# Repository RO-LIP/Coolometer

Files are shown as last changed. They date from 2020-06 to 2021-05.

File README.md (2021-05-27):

# Coolometer

A device, [inspired by Futurama](https://www.youtube.com/watch?v=tXb7gLe0zNk), to measure your coolness with a "real" AI.

## Components

This are the components we used. Alternatives might work also

- Raspberry PI Model 3 B+
- Raspberry PI Camera
- Micro Servo SG90
- MAX 4218CNG LED Matrix
- L9110 Motor Driver
- DC Motor 3V 16500 RPM 0.35A 130 Type
- Pizzo Speaker
- 3.5 mm Headphone Jack
- LY591-4 speaker
- PAM8403 Mini Amplifier
- Button
- 5V 2.1 A PowerBank for Power supply

### Wiring

Raspberry PI Model 3 B+ has enough ground Pins for all parts. Only one 5V pin has to be shared by the LED Matrix and the Servo motor.

<p align="center">
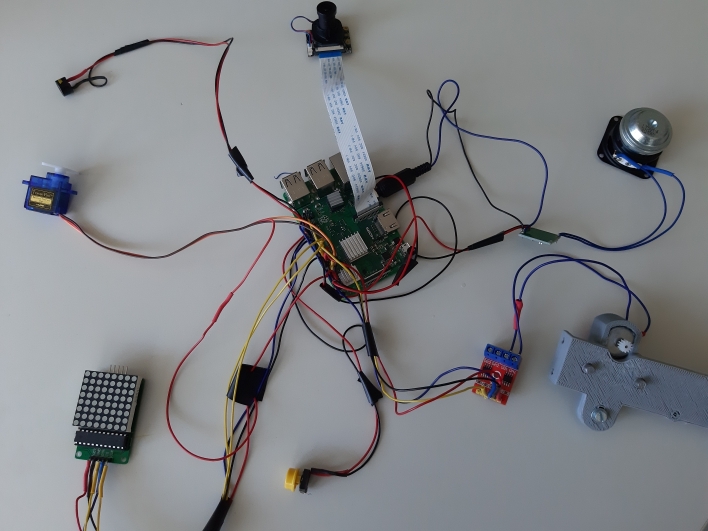
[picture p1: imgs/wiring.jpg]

</p>

#### Micro Servo SG90
One 5V shared with MAX 4218CNG LED Matrix<br/>
Data on GPIO 17 / PIN 11

#### MAX 4218CNG LED Matrix
One 5V shared with MAX 4218CNG LED Matrix<br/>
DIN on GPIO 10 / PIN 19<br/>
CS on GPIO 8 / PIN 24<br/>
CLK on GPIO 11 / PIN 23

#### L9110 Motor Driver
VCC on 3.3 <br/>
IA1 on GPIO 26 / PIN 37<br/>
IB1 on GPIO 20 / PIN 38

#### Pizzo Speaker
VCC on 3.3<br/>
GND on GPIO 36 / PIN 16

#### Headphone Jack / Amplifier
The Headphone Jack uses the Audio Out from the Raspberry PI.<br/>
Solder the longest PIN of the Jack to the "I" PIN of the Amplifier Board
Solder the second longest PIN longest PIN of the Jack to the "R" PIN of the Amplifier Board. We only use one Channel here.

Solder the R OUT PINs the the speaker.

Use one 5V Pin from the Raspberry PI to power the Amplifier Board

#### Button
VCC on 3.3 <br/>
GND to GPIO 18 / PIN 12

#### Camera
The camera is connected on the Raspberry Camera slot.

## Install
Set up a Raspberry PI with [Raspberry Pi OS Lite](https://www.raspberrypi.org/software/operating-systems/) 
[Enable SSH](https://www.raspberrypi.org/documentation/remote-access/ssh/) and connect via SSH to the Raspberry
Update System ( sudo apt full-upgrade)
Run sudo raspi-config:
- ADVANCED -> Resize File System
- SYSTEM  -> AUDIO -> Headphone Jack
- Interface -> Camera -> ON
- Interface -> SPI -> ON

Set System volume with 
```bash
sudo amixer -q -M sset Headphone 100%
```
Install depenendices:
```bash
sudo apt-get install python3-pip python3-venv python3-pygame 
libfreetype6-dev libjpeg-dev libopenjp2-7 libtiff5 libjpeg-dev libtiff5-dev libjasper-dev 
libpng12-dev libavcodec-dev libavformat-dev libswscale-dev 
libv4l-dev libxvidcore-dev libx264-dev qt4-dev-tools libatlas-base-dev 
libilmbase-dev libopenexr-dev libgstreamer1.0-dev libgirepository1.0-dev libcairo2-dev
```

Install Python dependencies:
```bash
python3 -m pip install --user --upgrade pip
python3 -m pip install --user virtualenv
python3 -m venv env
source env/bin/activate
pip3 install https://dl.google.com/coral/python/tflite_runtime-2.1.0.post1-cp37-cp37m-linux_armv7l.whl
pip install -r requirements.txt
```

Create Autostart:
```bash
sudo nano /etc/rc.local 
```
add:
```bash
sudo sh /home/pi/CoolOMeter/run.sh &
```

Now Reboot the system. When booting is finished, you will hear 2 short noises from the speaker.
You Coolometer should now work.

## 3D Print and Lasercut files
The Files are Available in the CAD-Zeichnungen folder.

## Usage

After you power your raspberry, it can take about 40 seconds to boot.
When the device is ready, the pizzo will make noise for a short time and the clockhand will go to zero.

Now press the button.

The clockhand will go to 50%  and the camera starts to search for a human face.

If the face is detected the clockhand will go to your coolness value and the pizzo will make noise according to the coolness.
If your coolness is 90% or higher, the thumb will come out and you will hear an "OH Yeah"

If your press the button again you will start from the beginning. 

HAVE FUN :)

## Train your own tensorflow lite model

The files contains our trained tensorflow lite model. The train data are our little secret. If you are not happy with it, here is a short description how to make your own model.

On your host machine with Linux, Python3 and pip:
```bash
pip3 install tensorflow
pip3 install tensorflow-hub[make_image_classifier]
```

Create a folder structure like the following one. And put picture into the cool / lame folder. Only JPG Files are allowed.
Base Folder
* coolometer (Folder)
    * cool (Folder)
        * img.jpg ...
    * lame (Folder)
        * img.jpg ..
* model (Folder)

In the Base folder call this command:
```bash
make_image_classifier   
--image_dir coolometer   
--tfhub_module https://tfhub.dev/google/tf2-preview/mobilenet_v2/feature_vector/4 
--image_size 224 
--saved_model_dir model/coolModel 
--batch_size 20  
--labels_output_file class_labels.txt 
--tflite_output_file tf_model_file.tflite
```
You can use other models if you exchange the tfhub_module link to something else from the [tensorflow hub ](https://tfhub.dev/). Make sure you adjuste the image_size to your choosen model.<br/>
In your base folder should now be a class_labels.txt and a tf_model_file.tflite file. Copy this to your Raspberry into the Coolometer folder.

If you have a new model, make sure to share it with us by open a pull request with your model data.

## Credits

Big thanks to the futurama creators comming up with this great Idea.
The OhYeah sound is from here: https://www.youtube.com/watch?v=c4c-egnkdLI

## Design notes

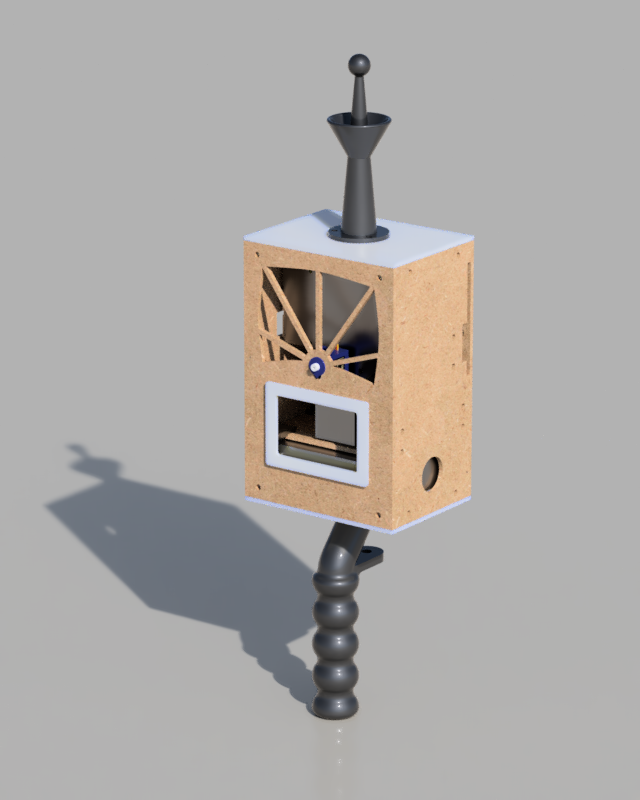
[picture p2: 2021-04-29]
CAD-Zeichungen/Coolometer_render.png

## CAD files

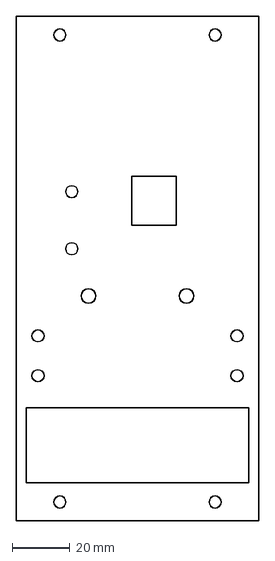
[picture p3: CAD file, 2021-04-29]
CAD-Zeichungen/DXFs for Laser Cutter/plate_left.dxf
84.0 x 175.0 mm

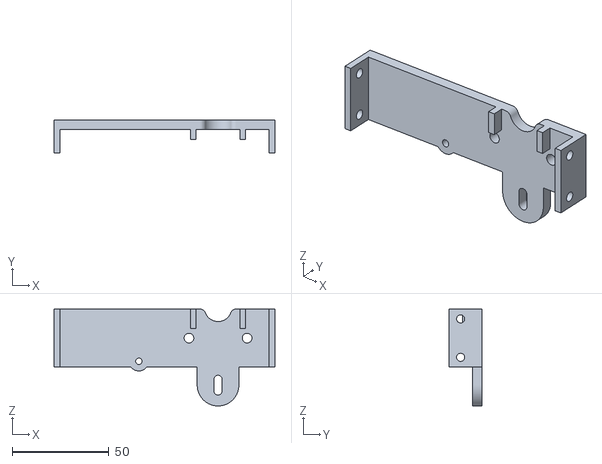
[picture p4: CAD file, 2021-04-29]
CAD-Zeichungen/STLs for 3D Printer/Bracket.stl
114.0 x 17.0 x 50.0

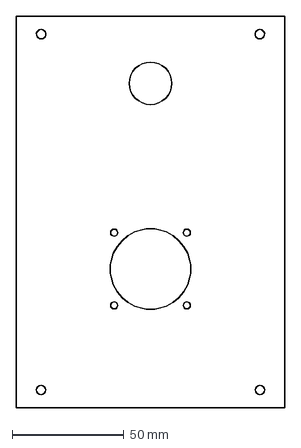
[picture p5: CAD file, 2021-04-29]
CAD-Zeichungen/DXFs for Laser Cutter/plate_front.dxf
120.0 x 175.0 mm

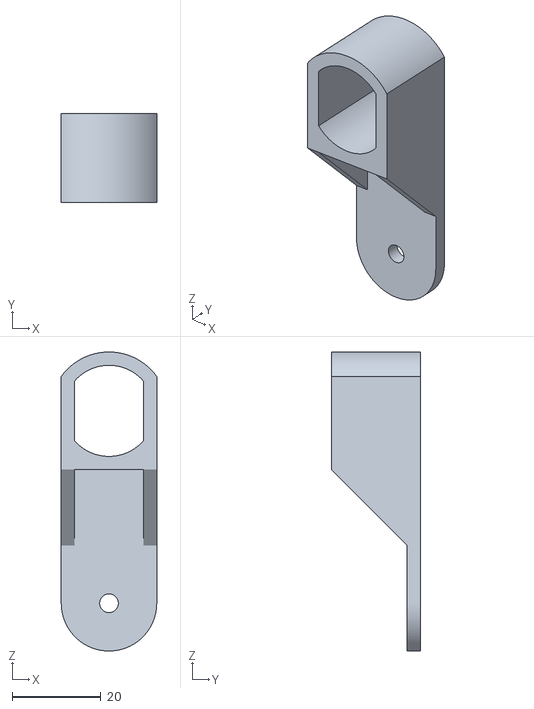
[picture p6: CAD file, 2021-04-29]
CAD-Zeichungen/STLs for 3D Printer/Motorbracket.stl
21.5 x 20.0 x 67.3

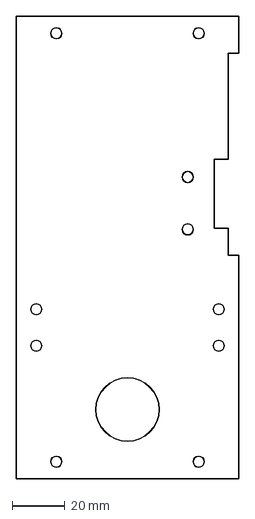
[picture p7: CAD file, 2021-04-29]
CAD-Zeichungen/DXFs for Laser Cutter/plate_right.dxf
84.0 x 175.0 mm

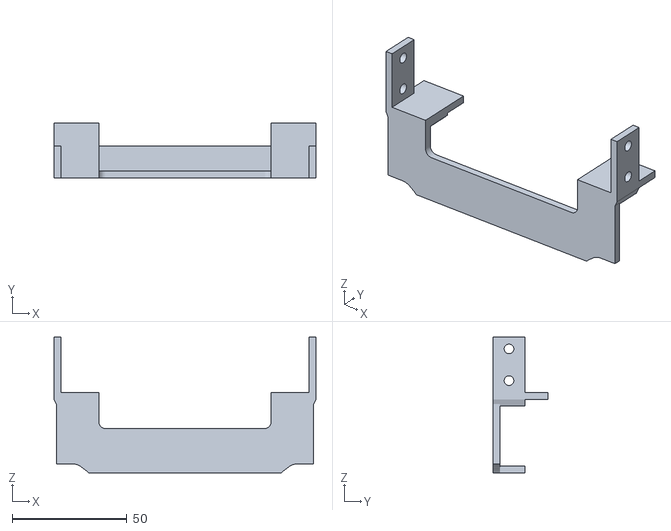
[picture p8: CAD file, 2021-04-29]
CAD-Zeichungen/STLs for 3D Printer/Poerbank mounting back.stl
114.0 x 24.0 x 59.0

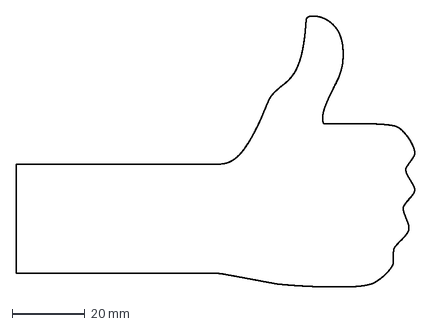
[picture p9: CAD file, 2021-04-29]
CAD-Zeichungen/DXFs for Laser Cutter/thumb.dxf
109.5 x 74.4 mm

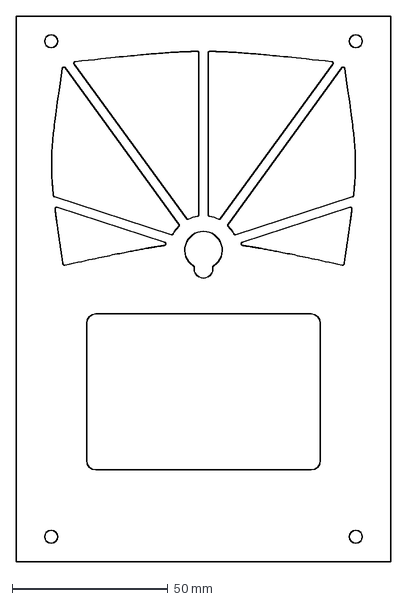
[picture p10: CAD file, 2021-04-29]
CAD-Zeichungen/DXFs for Laser Cutter/plate_back.dxf
120.0 x 175.0 mm

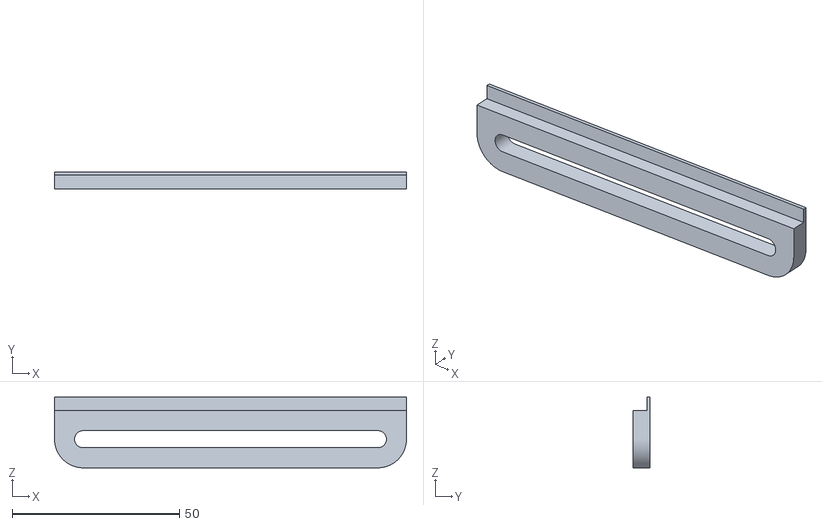
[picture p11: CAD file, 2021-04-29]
CAD-Zeichungen/STLs for 3D Printer/Thumb bracket.stl
105.1 x 5.20 x 21.1

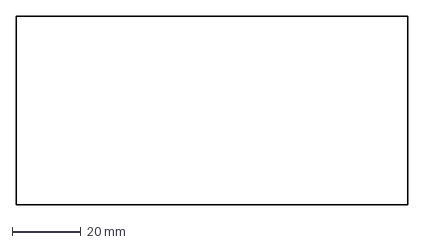
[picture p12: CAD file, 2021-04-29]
CAD-Zeichungen/DXFs for Laser Cutter/divider.dxf
114.0 x 55.0 mm

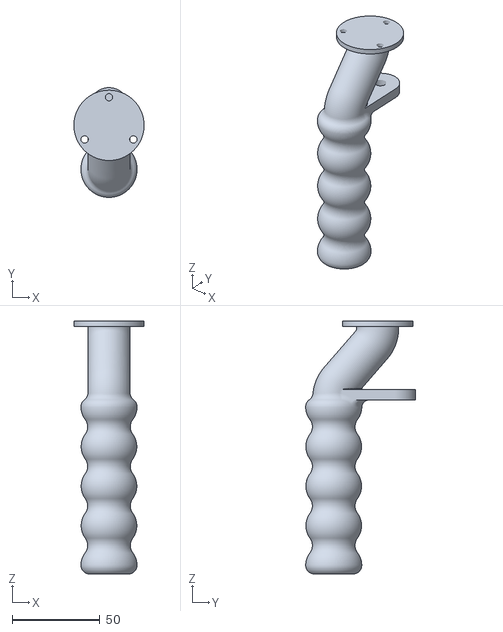
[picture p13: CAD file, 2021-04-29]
CAD-Zeichungen/STLs for 3D Printer/Handle.stl
40.0 x 62.5 x 144.0

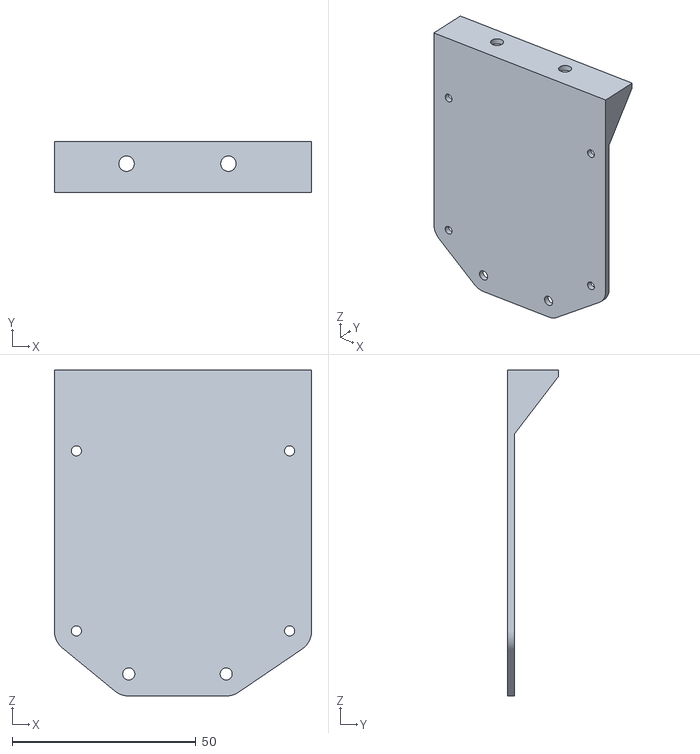
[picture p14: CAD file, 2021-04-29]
CAD-Zeichungen/STLs for 3D Printer/Circuit board mounting.stl
70.0 x 13.8 x 88.7

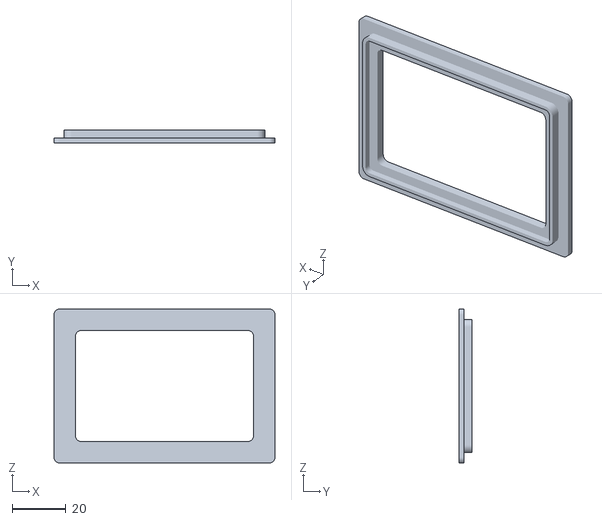
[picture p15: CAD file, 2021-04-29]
CAD-Zeichungen/STLs for 3D Printer/LED Frame.stl
82.2 x 5.00 x 57.2

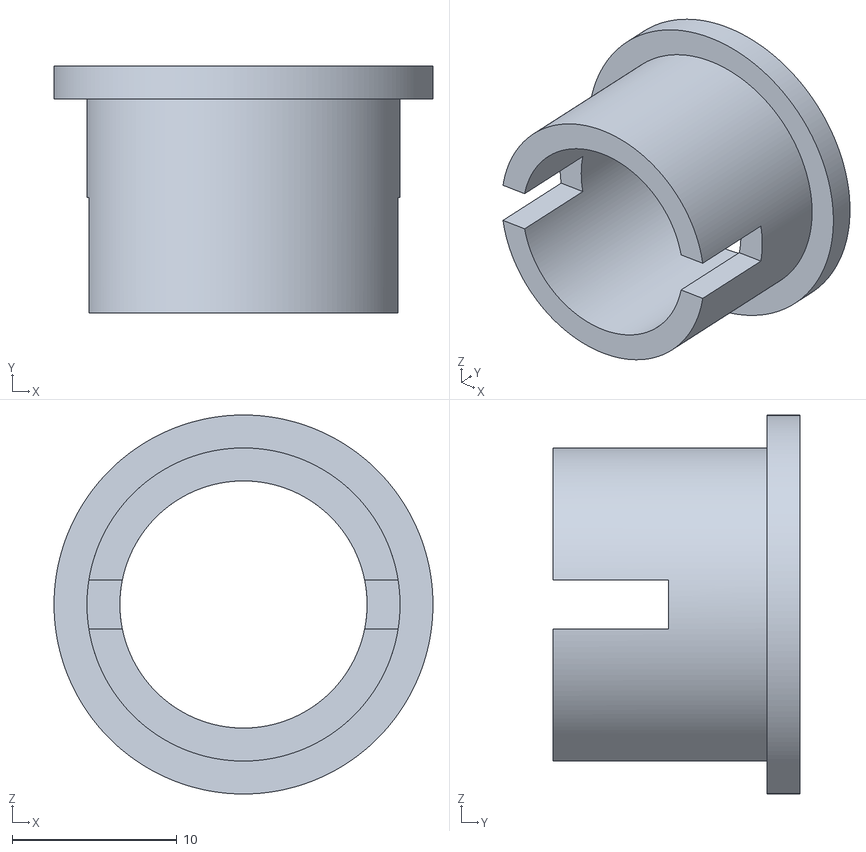
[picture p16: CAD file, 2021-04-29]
CAD-Zeichungen/STLs for 3D Printer/Camera mounting.stl
23.0 x 15.0 x 23.0

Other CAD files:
CAD-Zeichungen/STLs for 3D Printer/Poerbank mounting front.stl
CAD-Zeichungen/STLs for 3D Printer/Antenne.stl
CAD-Zeichungen/STLs for 3D Printer/Plate downside.stl
CAD-Zeichungen/STLs for 3D Printer/Plate upside.stl

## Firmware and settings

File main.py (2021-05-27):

import time
from multiprocessing import Process, Value

import servo 
import switch
import camera
import speaker
import motor
import LEDMatrix
import piezo
import messure

import RPi.GPIO as GPIO




if __name__ == '__main__':

    piz = piezo.Piezo(16)
    print("Piezo init")
    pointer = servo.Servo(17)
    print("Servo init")
    sw = switch.Switch(18)
    print("Switch init")
    cam = camera.camera()
    time.sleep(0.1)
    print("Camera init")
    speak = speaker.speaker("OhYeah.mp3")
    print("Speaker init")
    mot = motor.motor()
    print("Motor init")
    matrix = LEDMatrix.LEDMatrix()
    print("LEDMatrix init")
    mes = messure.messure()
    print("messure init")
    #start piezo in parallel
    time.sleep(0.1)
    pizWait = Value('d', 0.4)
    p = Process(target=piz.trigger, args=(pizWait,))
    p.start()
    print("Task init")
    coolness = 0
    time.sleep(1.0)

    try:
        while True:
    # cleanup
            coolness = 0
            pizWait.value = 0.0 
            time.sleep(0.1)
            matrix.clear()
            print("Matrix clear")
            time.sleep(0.1)
            pointer.setservo(0)
            print("Servo clear")
            print("Motor clear")
            time.sleep(0.1)
            mot.inside()
    # wait for Sitch
            sw.waitForSwitch()
            pointer.setservo(90)
    #if pressed
            cam.takePicture()

            coolness = mes.getCoolness()
            print(coolness)

    # show coolness
            pizWait.value = coolness
            pointer.setservo((1-coolness) * 180)
            
    # if someone is extremly cool
            if coolness >= 0.9:
                time.sleep(0.3)
                mot.outside()
                time.sleep(0.6)
                speak.playSound()
                time.sleep(1) 
                matrix.show()

                
                
    # restart on switch
            sw.waitForSwitch()
        


    except KeyboardInterrupt:
    # Abbruch mit [Strg][C],
    # Servo auf 0 Grad, PWM beenden
        pointer.cleanup()
        p.join()

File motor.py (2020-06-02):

import sys
import time
import RPi.GPIO as GPIO



class motor:
    def __init__(self):
        self.IsOutside = True
        GPIO.setup(26, GPIO.OUT,initial=False)
        GPIO.setup(20, GPIO.OUT,initial=False)
        self.forward = GPIO.PWM(26, 100)
        self.backward = GPIO.PWM(20, 100)
        

    def outside(self):
        if self.IsOutside == True:
            return
        time.sleep(0.5)
        self.forward.start(35)
        time.sleep(0.5)
        self.forward.stop()
        time.sleep(0.5)
        self.IsOutside = True

    def inside(self):
        if self.IsOutside == False:
            return
        time.sleep(0.5)
        self.backward.start(35)
        time.sleep(0.5)
        self.backward.stop()
        time.sleep(0.5)
        self.IsOutside = False

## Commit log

2020-03-06 Added CAD-Files
2021-04-29 Added DXF and STL files
    [Antenne.stl, Bracket.stl, Camera mounting.stl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]
2021-05-27 Extended Readme + Small fixes
    [main.py]
